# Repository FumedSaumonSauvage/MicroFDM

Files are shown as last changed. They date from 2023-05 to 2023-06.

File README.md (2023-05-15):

# MicroFDM
Cheap, compact, mostly 3D printed FDM printer designed to be printable on an Ender 3.
</br>
Uses an upside-down design to be folded easily, and a coreXY architecture to be as compact as possible. This project is designed to reuse as much parts from an ender 3 after popular mods to reuse them, such as the motherboard and fans from a silent mod, extruder from a direct extrusion mod and others. In short, minimal amount of money wasted.
</br>
It's all printable on an ender 3 (mine modified but cant see why it wouldn't be possible on a stock one) so every printer will do fine, in theory in less than 1 kg of PETG (still not finished my roll with a lot of testing done. Expect around 400 gr of material if you have a low print failure rate. Everything that is not in this repository (some pulleys, timing belts & gears) are not my work and can be found on Thangs. I may get them here if their licences permit it. As everything is 3d printed on a classic bedslinger printer, I plan to have approx 100 x 100 x 100 mm of print space on the resultant printer.
</br>

<ul> Bill of materials as of 15/05, everything is to be sourced on aliexpress:
<li> Some 8mm linear rods, preferably 2* 400 mm : about 10 €. You will need a saw to cut them.</li>
<li> 15 mm MGN12 linear rail : about 5€</li>
<li> 24V 3A PSU, about 12€</li>
<li> Creality ender 3 hotend : about 10€. If you modded your printer with a V6 hotend (or other), you already have it.</li>
<li> 1m of PTFE tubing : around 1€.</li>
<li> linear endless screw for the Z axis : around 5€</li>
<li> Titan extruder gear: about 2€. Stock creality extruder is extremely bad so I chose to redesign a printable titan extruder reusing parts of the crality one. It's my design, so it possibly sucks even more than the original creality, but there's always room for improvements.</li>
<li> Trianglelab MR85ZZ bearings for the extruder</li>
<li> Some LM8UU linear bearings : approx. 3€ for 2 bearings.</li>
<li> A motherboard. Mine is a creality 4.2.2, around 25€ if you buy it (don't) but any will do. If you've done a silent mod, you probably have one laying around.</li>
<li> Some fans: a 60mm 24V for PSU & motherboard, and a 40mm 24V for the hotend. Pro tip : 60 mm 24V fans can be found inside ender 3 PSUs, again you have one if you modded your ender 3 to be silent.</li>
<li> 4 stepper motors (3 axis and one extruder) : approx. 35€ for some weak pankakes ones, should be sufficient. Mine are Usongshine 17HS4023, as the extruder is a titan it doesn't require more torque.</li>
<li> You will probably need some terminal kits, it's about 3€ each. Add 25€ for special pliers, or just suffer for free through each connectors with regular pliers! Choose the second option, you don't need special crimping pliers.</li>
<li> Buy a screen and a knob if you needit (around 15€), but I will be running everything from a computer.</li>
<li> One bed sticker for the bed. Did not fully design the bed yet, so i'm not giving any references.</li>
<li> Ordered some other components for the Z axis too, but still in progress.</li>
</ul>

Progression as of last update of readme:
First print, works but not well.
progression

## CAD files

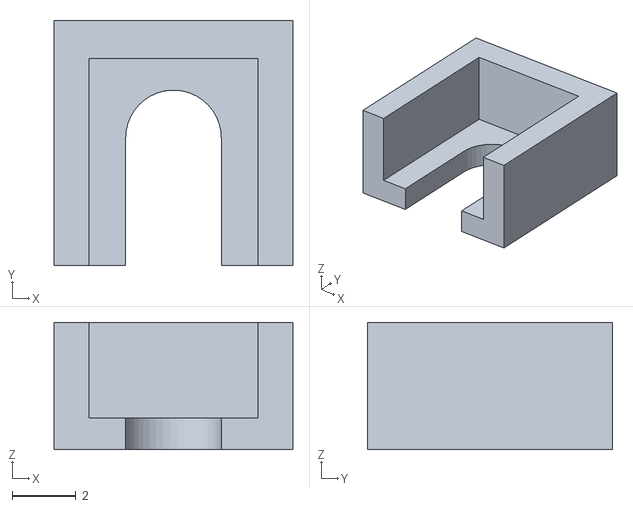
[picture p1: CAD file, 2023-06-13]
maintien ecrou.stl
7.50 x 7.70 x 4.00

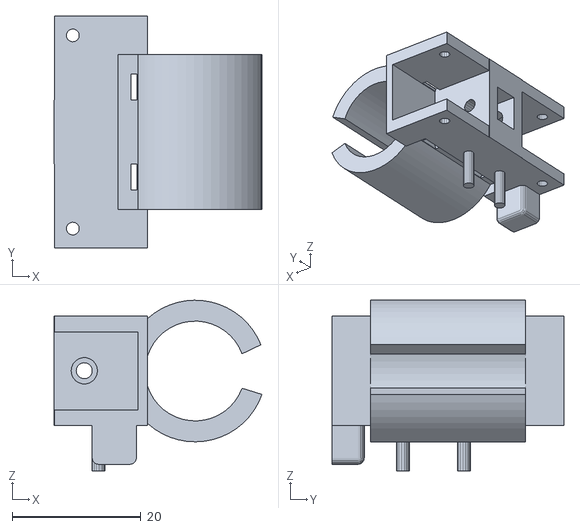
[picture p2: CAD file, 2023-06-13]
support axe X v4.1.stl
32.3 x 36.0 x 26.5

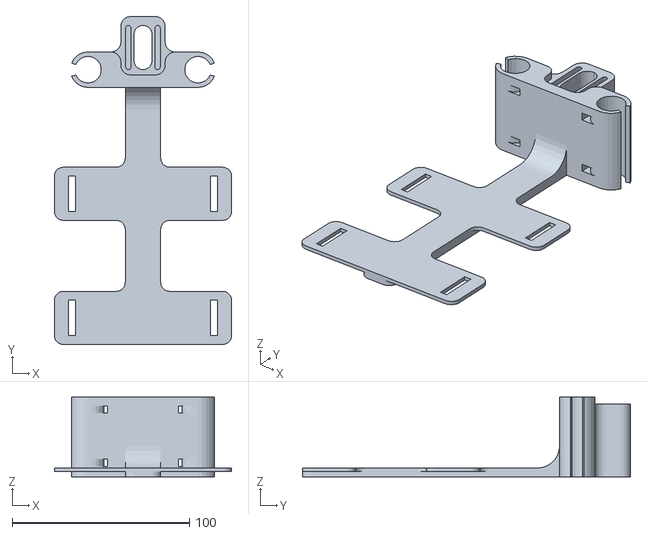
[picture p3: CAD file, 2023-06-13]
support lit v4.1.stl
100.0 x 185.0 x 45.0

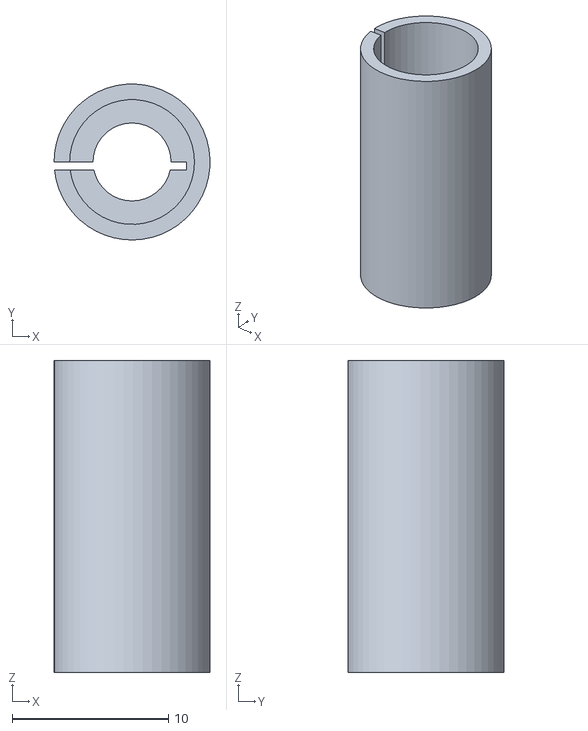
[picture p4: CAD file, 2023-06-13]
liaison Z.stl
9.99 x 10.00 x 20.0

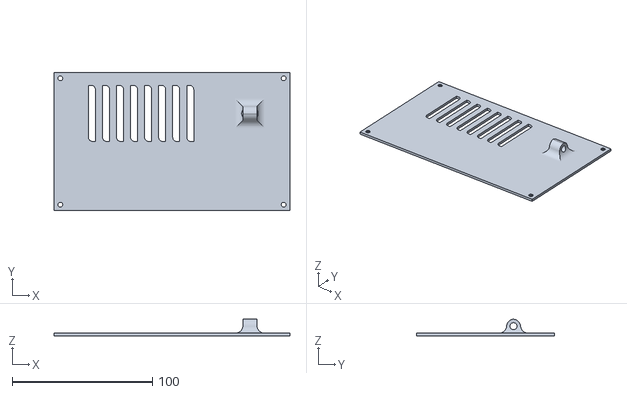
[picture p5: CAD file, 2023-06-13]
couvercle boitier v3.stl
168.0 x 98.4 x 11.9

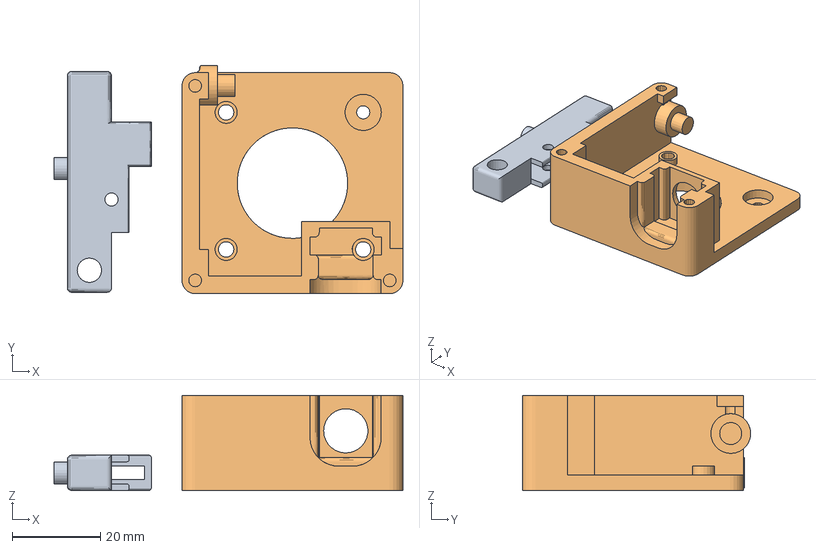
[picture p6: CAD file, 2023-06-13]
bras extrudeur v18.3mf
78.9 x 51.6 x 21.5 mm
bras extrudeur v18
Corps extrudeur v18

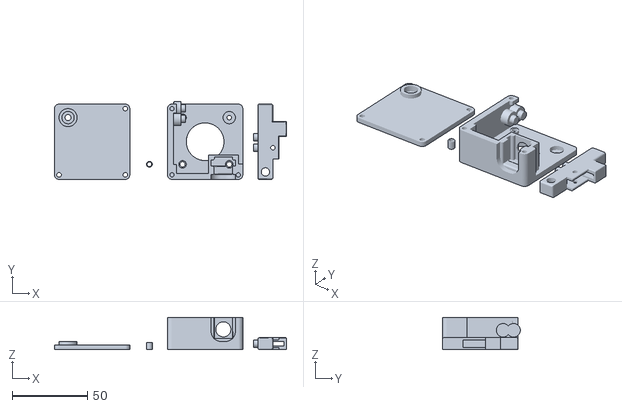
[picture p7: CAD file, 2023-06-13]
extrudeur v17.stl
154.0 x 51.6 x 21.5

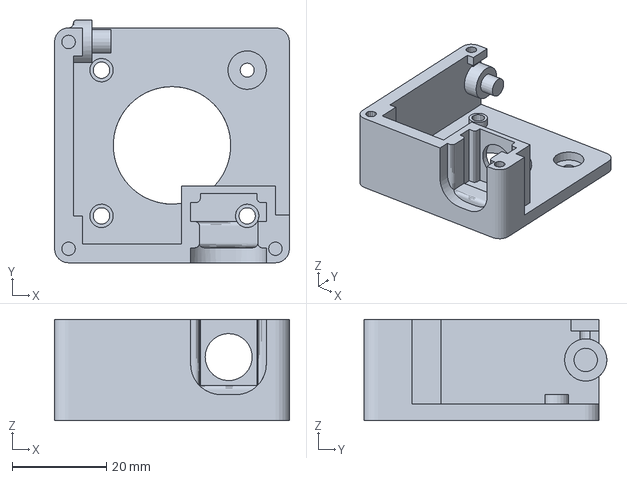
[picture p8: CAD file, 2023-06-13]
Corps extrudeur v18.3mf
50.0 x 51.6 x 21.5 mm

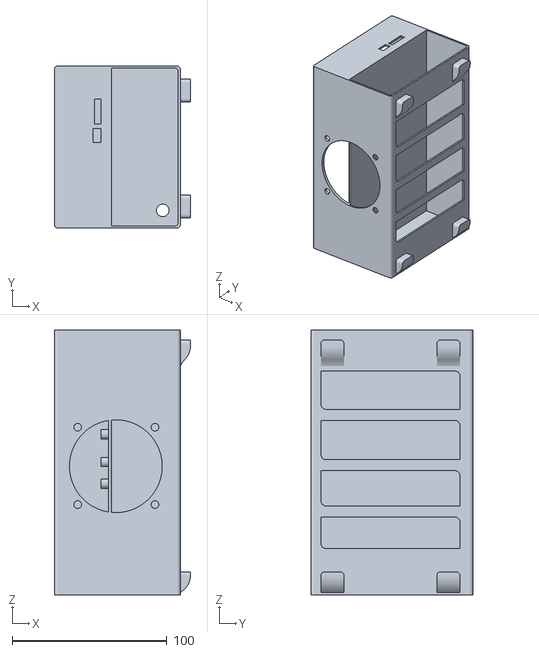
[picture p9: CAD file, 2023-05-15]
boitier alim mobo v5.stl
88.0 x 104.8 x 171.4

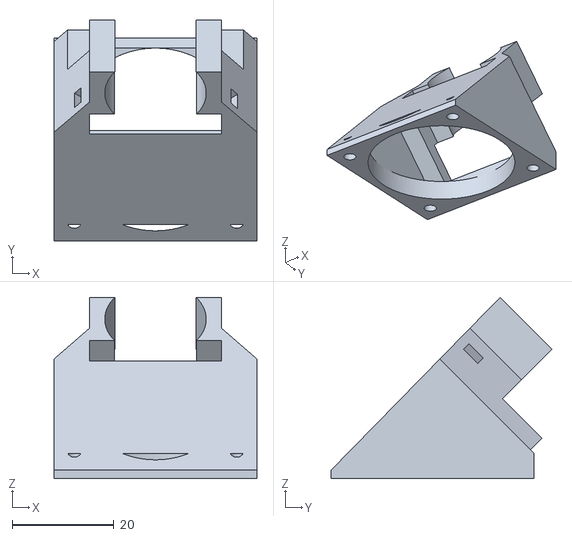
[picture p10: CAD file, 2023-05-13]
support ventilo v2.stl
40.0 x 43.5 x 35.7

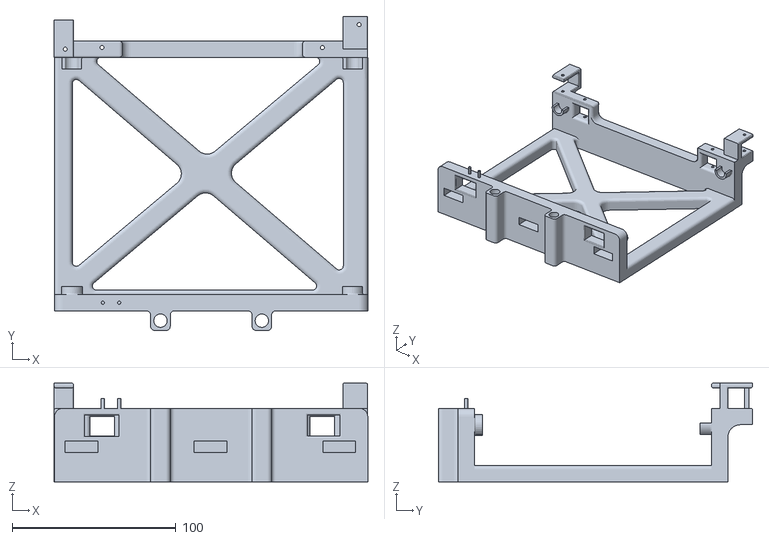
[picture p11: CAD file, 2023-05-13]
support structure cross v8.stl
191.8 x 192.0 x 60.5

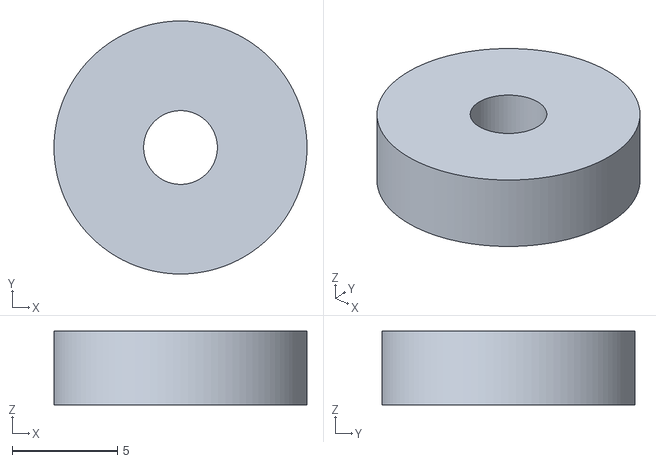
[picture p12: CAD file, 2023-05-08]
damper v2.stl
12.0 x 12.0 x 3.50

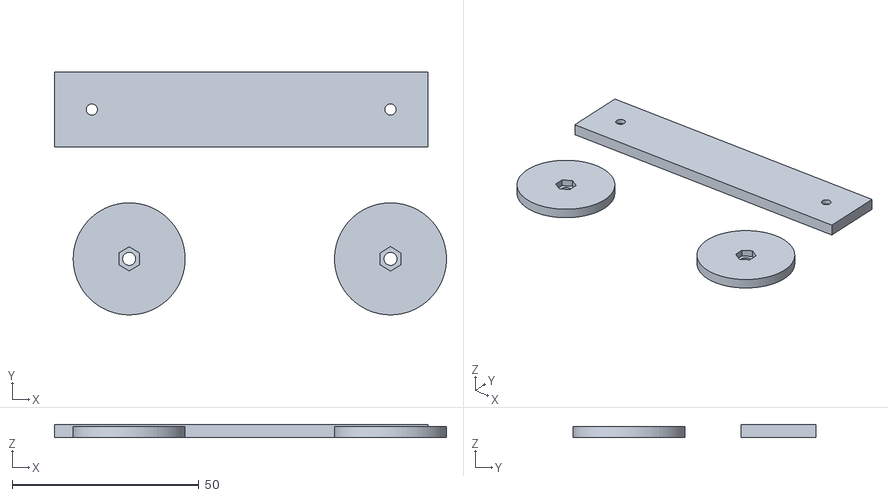
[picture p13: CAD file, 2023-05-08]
lit v1.stl
105.0 x 65.0 x 3.50

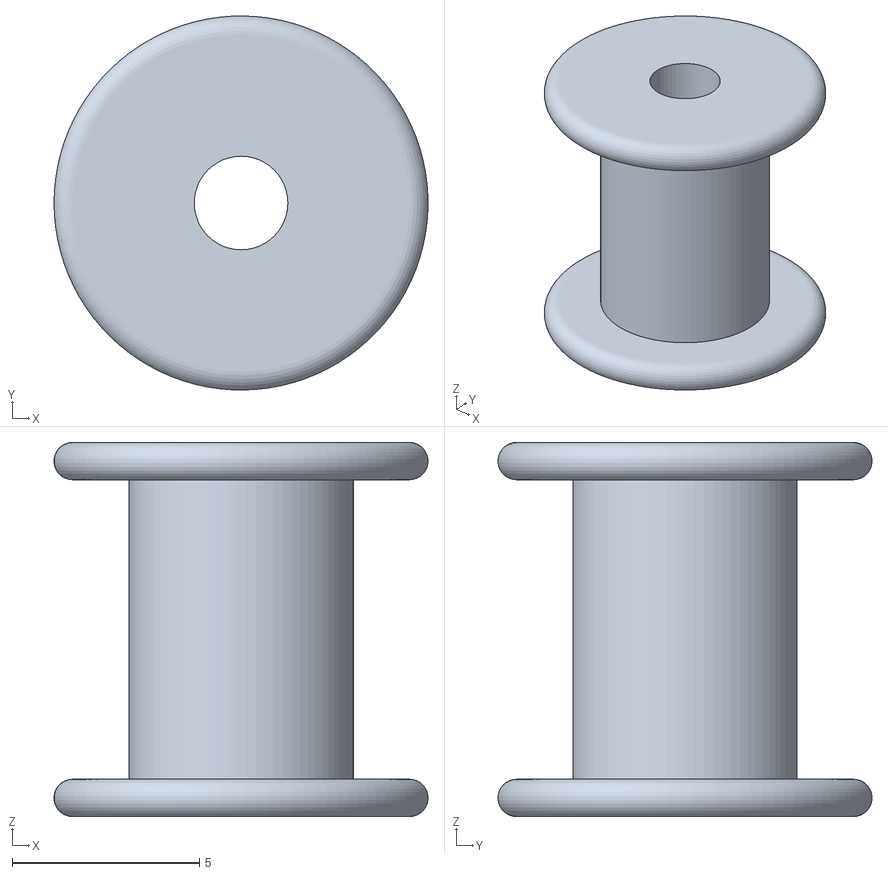
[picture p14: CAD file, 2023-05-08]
Roulette 1 v5.stl
9.99 x 9.99 x 10.0

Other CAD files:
support stepper Z.stl
Coude hotend v3.stl
guide filament v5.stl
chariot v4.stl
Roulette 1 v1.stl
Roulette 1 v5 (archive).f3d
boitier alim mobo v5.f3d
extrudeur v15.stl
grosse roulette v3.stl
guide filament v5 (archive).f3d
support stepper v2 (archive).f3d
support stepper v2.stl
support stepper v3.f3d

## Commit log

2023-04-28 ajout de roulettes en stock
    [Roulette 1 v1.stl, grosse roulette v3.stl]
2023-04-28 ajout du boitier, ventilateur du bon côté cette fois
    [boitier alim mobo v3.step, boitier alim mobo v3.stl]
2023-04-28 ajout de structure sans plateau, axe X et sup stepper
    [structure v6.stl, support axe X v3.stl, support stepper v2.stl]
2023-04-28 changement rapido axe X pour mettre des endstops
    [support axe X v3.stl, support axe X v4.step, support axe X v4.stl]
2023-04-28 rapprochement des barres du chariot, ajout testfit hotend et extension endstop
    [chariot v3.stl]
2023-04-29 la hotend est maintenant fixable sur le chariot avec une zip tie
    [chariot v3.stl, chariot v4.stl]
2023-04-29 ajout d'un adaptateur pour le bowden, version pas testée
    [Coude hotend v2.stl]
2023-05-01 design de l'extrudeur fini, quelques ajustements à faire mais ca a l'air de fonctionner(v10)
    [extrudeur v10.stl, guide filament v3.stl]
2023-05-01 décalage roue + agrandissement vis fixation + collision avec guide parfois
    [extrudeur v10.stl, extrudeur v12.stl, guide filament v3.stl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]
2023-05-01 mal lu la datasheet du stepper, correction de la taille des empreintes de fixation
    [extrudeur v12.stl, extrudeur v13.stl]
2023-05-01 allongement guide + fix cover
    [extrudeur v13.stl, extrudeur v15.stl, guide filament v4.stl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]
2023-05-01 élongation du coude pour éviter la collision avec l'axe
    [Coude hotend v2.stl, Coude hotend v3.stl]
2023-05-05 ajout d'une archive pour support stapper du coté, et nouveua modele de support pour Z
    [support stepper Z.stl, support stepper v2 (archive).f3d]
2023-05-08 ajout d'archives et de roulettes pour faire de la place
    [Roulette 1 v5 (archive).f3d, Roulette 1 v5.stl, guide filament v5 (archive).f3d]
2023-05-08 début du prototypage du lit
    [damper v1.stl, lit v1.stl]
2023-05-08 ajustements lit et ajout structure de maintien
    [damper v1.stl, damper v2.stl, support lit v3.stl]
2023-05-13 ajout ventilo hotend et structure finale
    [structure v6.stl, support structure cross v8.stl, support ventilo v2.stl]
2023-05-15 corps de l'imprimante fini
    [boitier alim mobo v3.step, boitier alim mobo v3.stl, boitier alim mobo v5.f3d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]
2023-06-13 ajout de plein de trucs, nettoyage plus tard
    [Corps extrudeur v18.3mf, bras extrudeur v18.3mf, couvercle boitier v3.stl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]
2023-06-13 séparation du support lit et de l'attache z
    [liaison Z.stl, support lit v4.1.stl, support lit v4.stl]
2023-06-13 révision axe X pour éviter de coller le microswitch
    [support axe X v4.1.stl, support axe X v4.step, support axe X v4.stl]
